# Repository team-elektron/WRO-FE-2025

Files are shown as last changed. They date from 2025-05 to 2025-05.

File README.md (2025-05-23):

# Elektron Team - WRO Future Engineers 2025

## Content

* `t-photos` contains 2 photos of the team (an official one and one funny photo with all team members)
* `v-photos` contains 6 photos of the vehicle (from every side, from top and bottom)
* `video` contains the video.md file with the link to a video where driving demonstration exists
* `schemes` contains schematic diagrams of the driving base.
* `src` contains code of control software for all components which were programmed to participate in the competition.
* `models` is for the files for models used by 3D printers to produce the vehicle elements.
* `other` is for other files which can be used to understand how to prepare the vehicle for the competition.

## Introduction

This is the public repository for our team and the work we have done on our robot.

<p float="left">
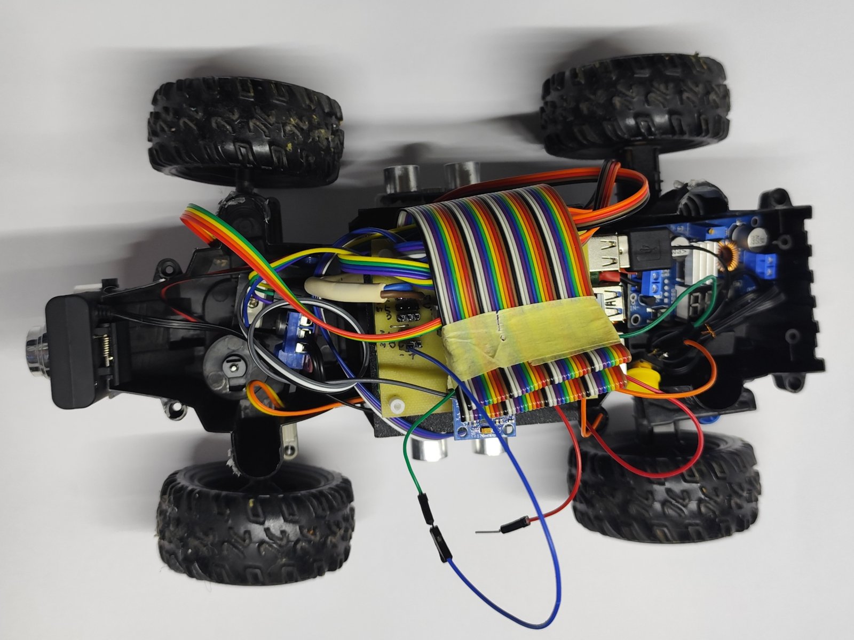
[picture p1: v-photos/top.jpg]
  
  &nbsp;
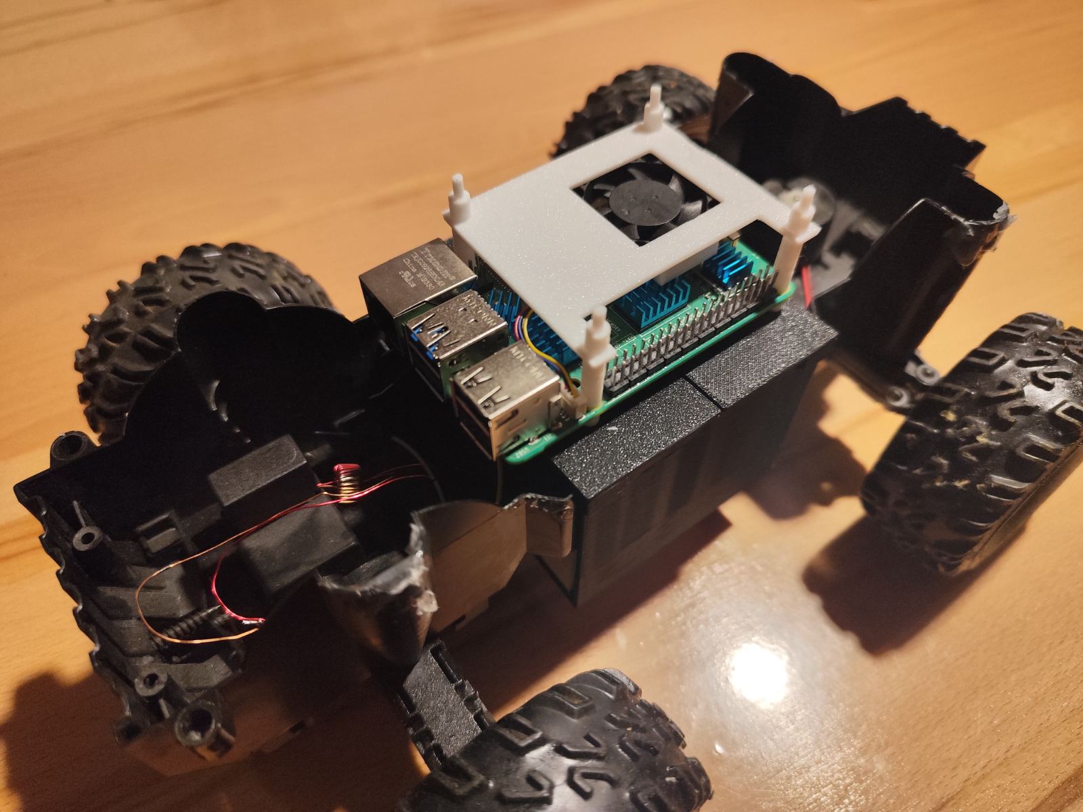
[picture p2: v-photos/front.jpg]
  
</p>

## Design elements

### Technical specifications
- Power: 3s1p Li-Ion Battery (EVE ICR18650-26v)
- Control: Raspberry Pi 5 8GB SBC
- Movement: Brushed motor
- Sensors: 3x Ultrasonic sensors, Camera

### Driving elements

For the driving base we have chosen a pre-made RC car driving base due to a lack of time. The steering and main driving motors are controled by a L298N Motor H-Bridge controller. 

<p float="left">
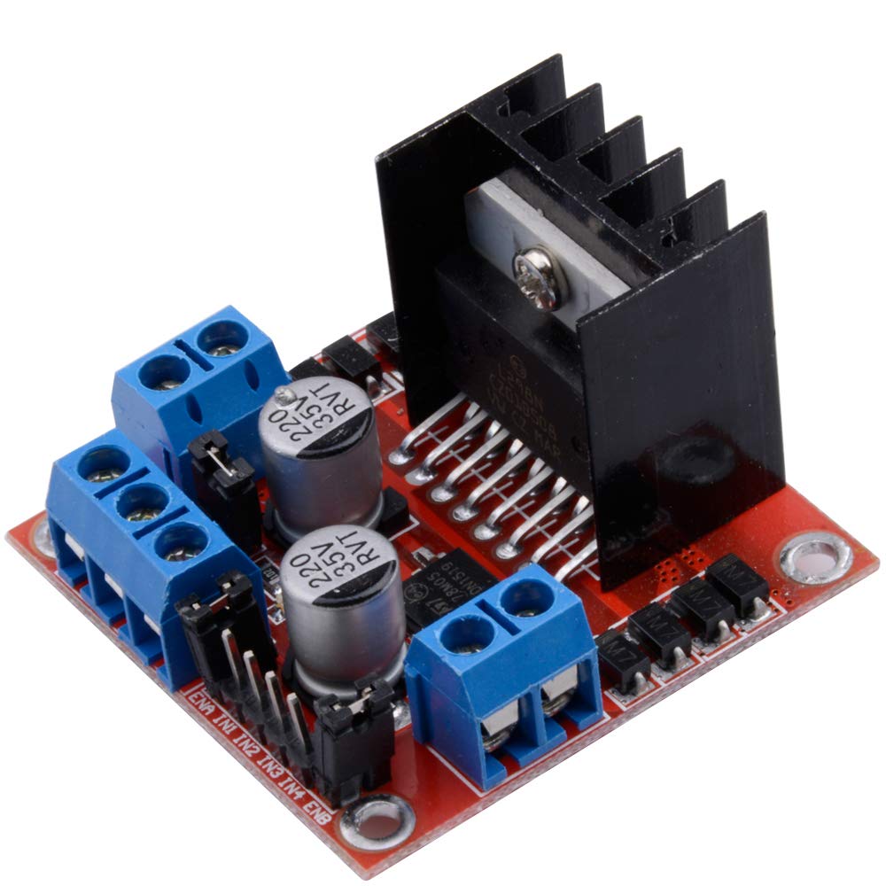
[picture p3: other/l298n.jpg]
  
</p>

### Cameras & Sensors

On our robot we have utilised a MPU-6050 IMU sensor for detecting the rotation angle when steering. 
The "eyes" of the operation are a set of 3 HC-SR04 Ultrasonic sensors and a standard USB Webcam.

<p float="left">
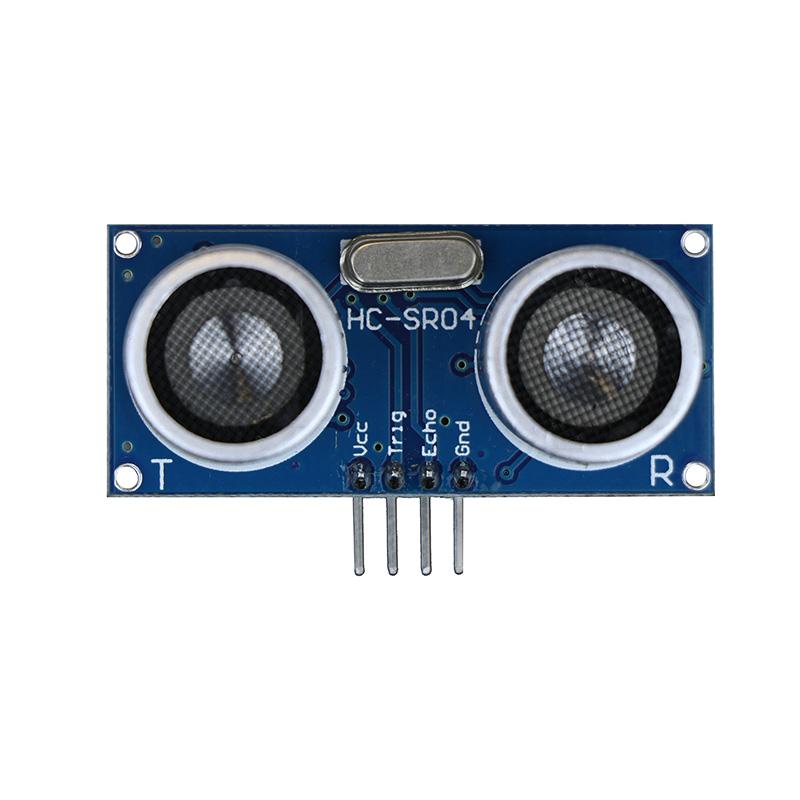
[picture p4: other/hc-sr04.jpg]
  
  &nbsp;
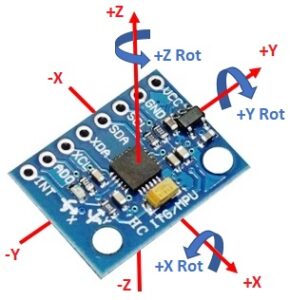
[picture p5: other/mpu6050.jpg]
  
  &nbsp;
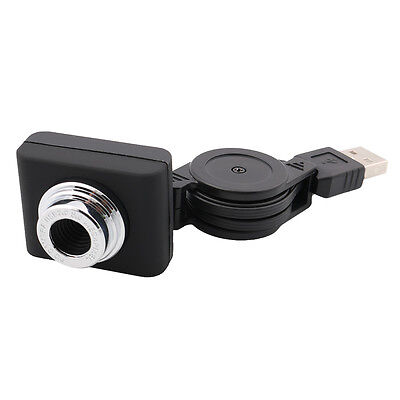
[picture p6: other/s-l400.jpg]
  
</p>

### Power supply and control elements

For the power supply we chose a custom made 18650 based battery in the 3s1p configuration which can be quickly charged with USB-C. 
This gives us around 27.5Wh (2.5Ah @ 10.8v nominal) to work with which is plenty for the job at hand.

<p float="left">
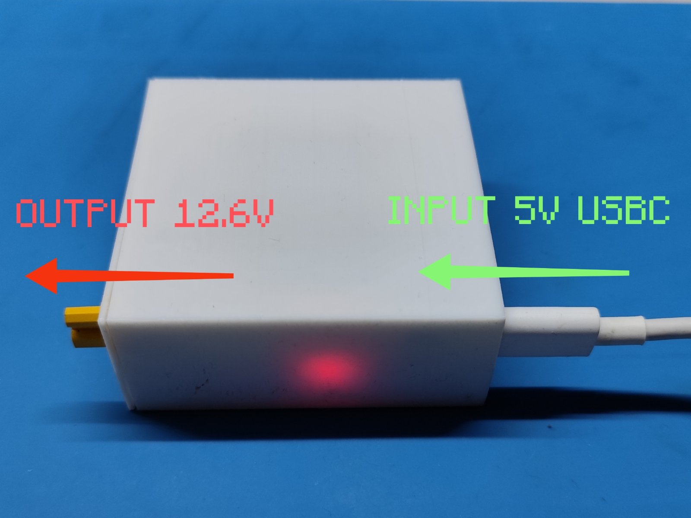
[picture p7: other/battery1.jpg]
  
  &nbsp;
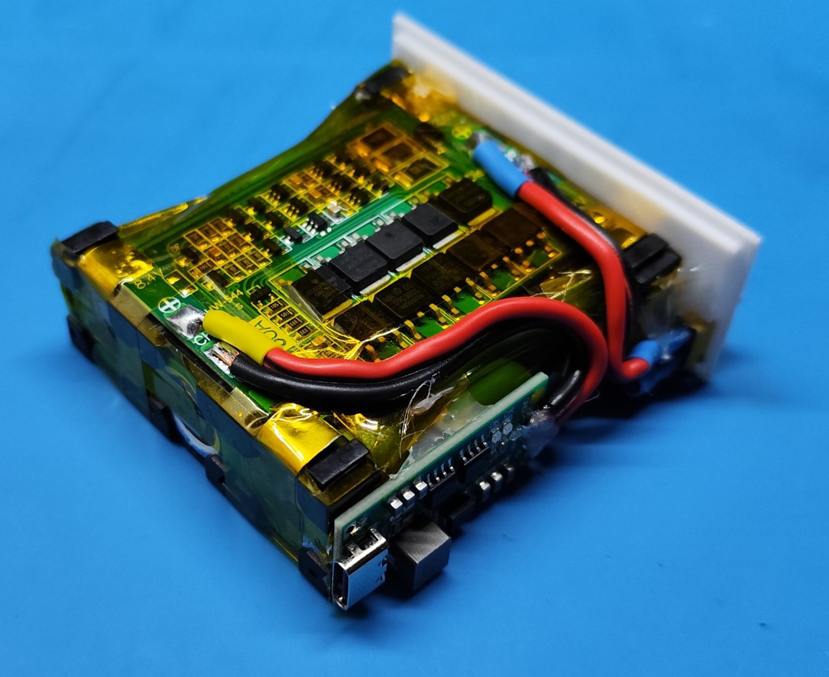
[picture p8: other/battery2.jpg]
  
</p>

The robot is based on a Raspberry Pi 5 which requires a stable power input of 5v @ 5A, for this job we have first chosen an UBEC voltage regulator, but due to the specific adapter we got not actually being able to handle the Pi, we had to switch to a more readily available replacement, the XL4015.

<p float="left">
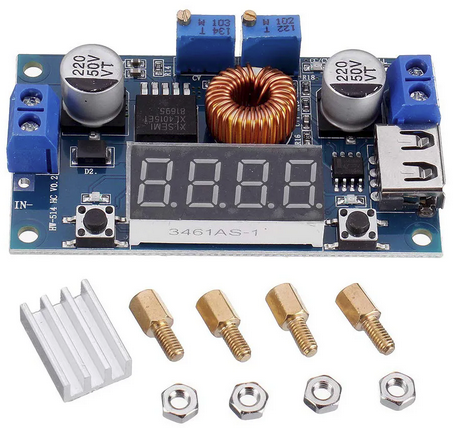
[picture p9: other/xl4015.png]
  
  &nbsp;
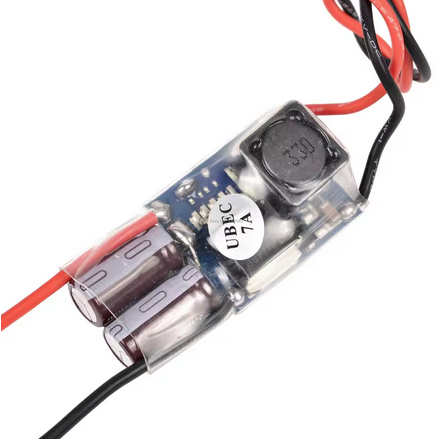
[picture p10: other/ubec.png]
  
</p>

We have designed a custom Pi GPIO shield to more easily wire up all of our power sources and sensors. The design for this PCB can be found in the schemes folder.

<p float="left">
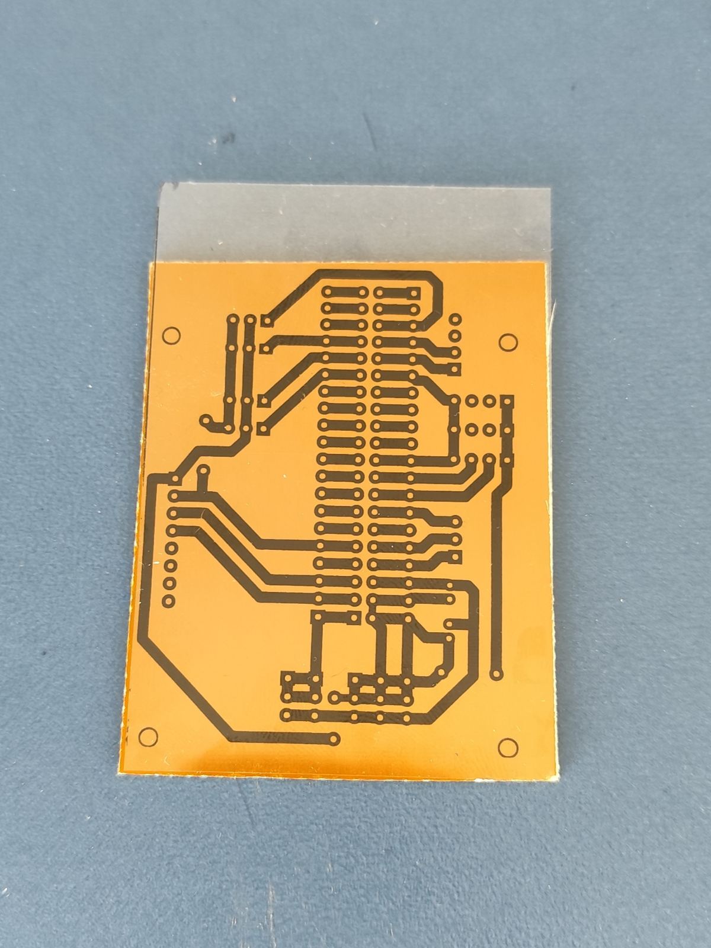
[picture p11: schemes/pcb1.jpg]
  
  &nbsp;
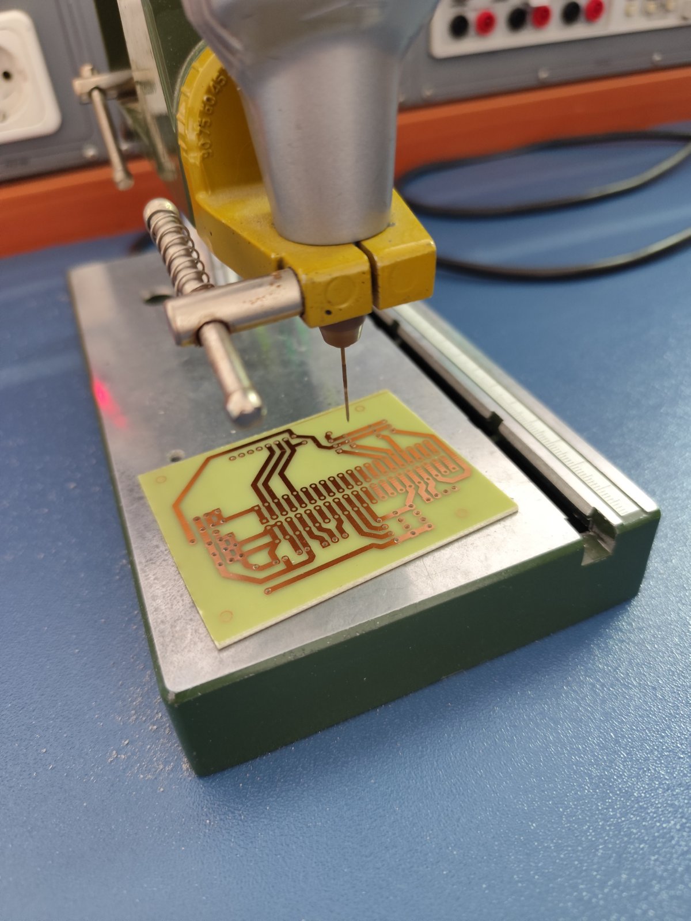
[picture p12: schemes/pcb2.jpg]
  
  &nbsp;
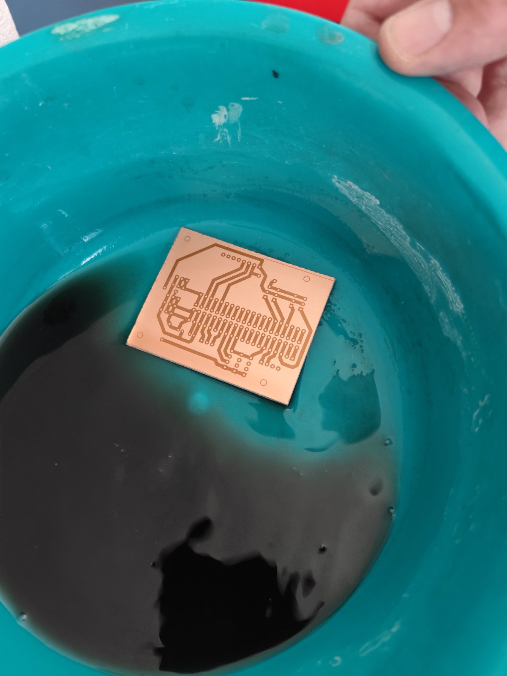
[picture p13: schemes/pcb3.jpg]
  
  &nbsp;
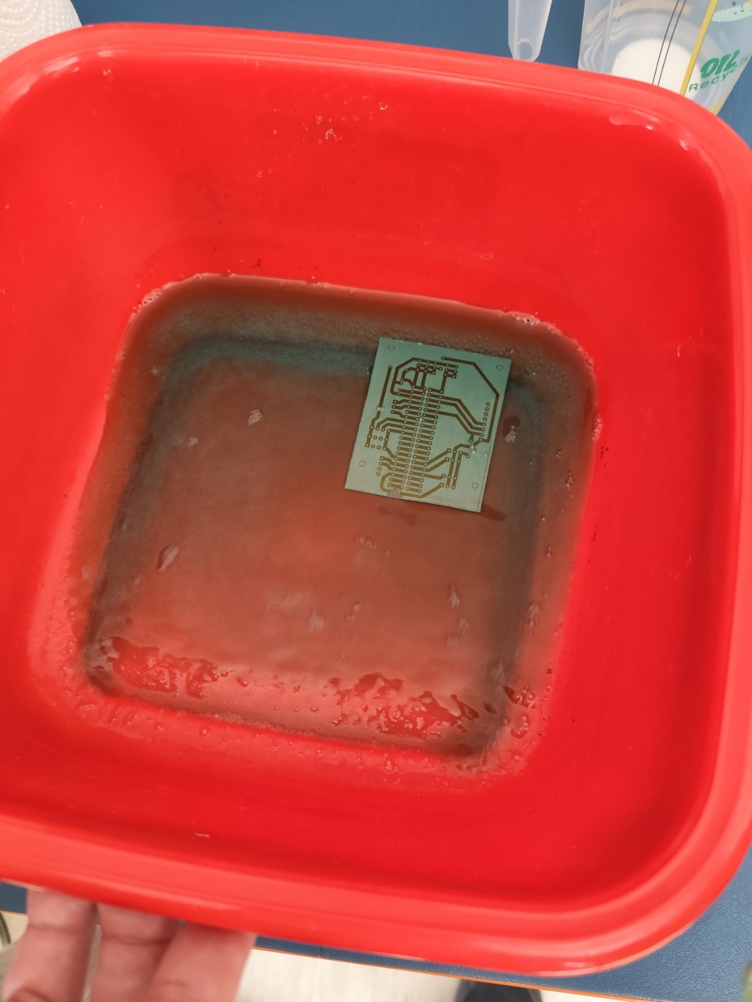
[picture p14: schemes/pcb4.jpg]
  
</p>

### Code

We have written our code in C++ using the WiringPi library for interfacing the Pi GPIO. 
You can find the code in the src folder and the instructions on how to use it.

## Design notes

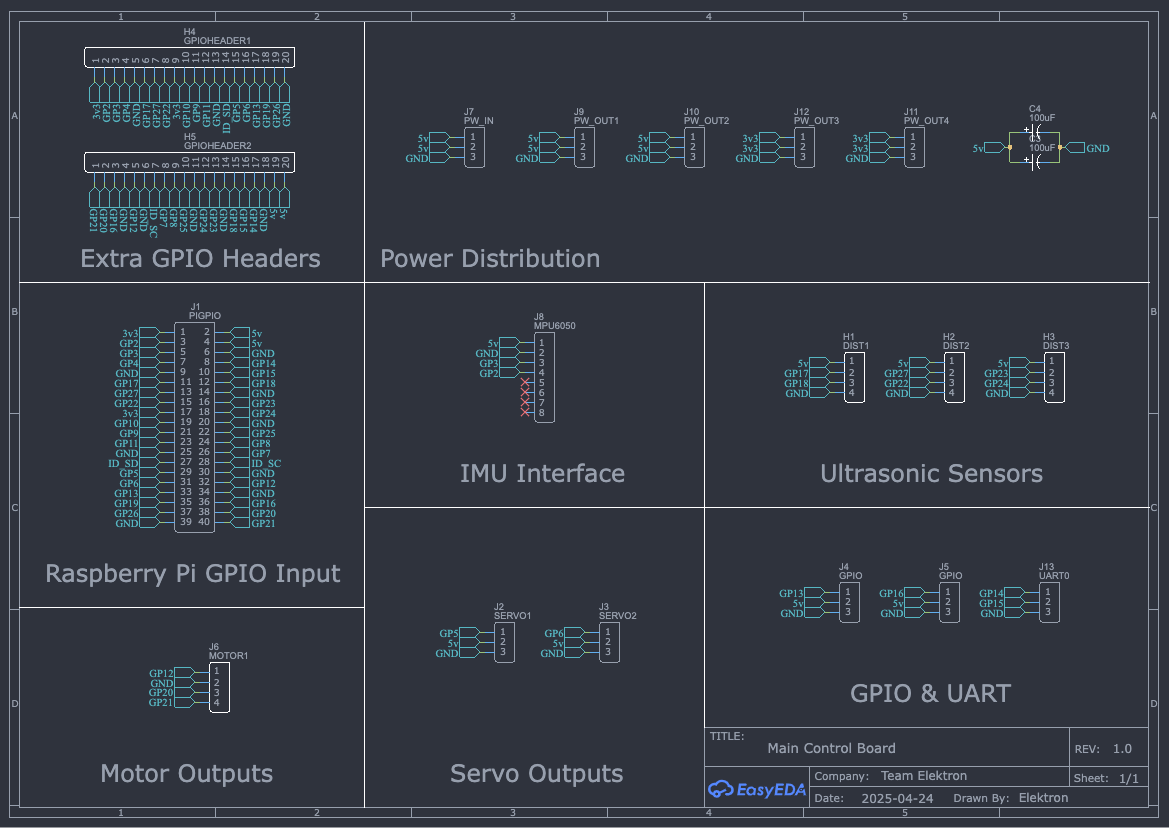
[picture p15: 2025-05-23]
schemes/Schematic_WRO FE Robot Control Board_2025-04-24.png

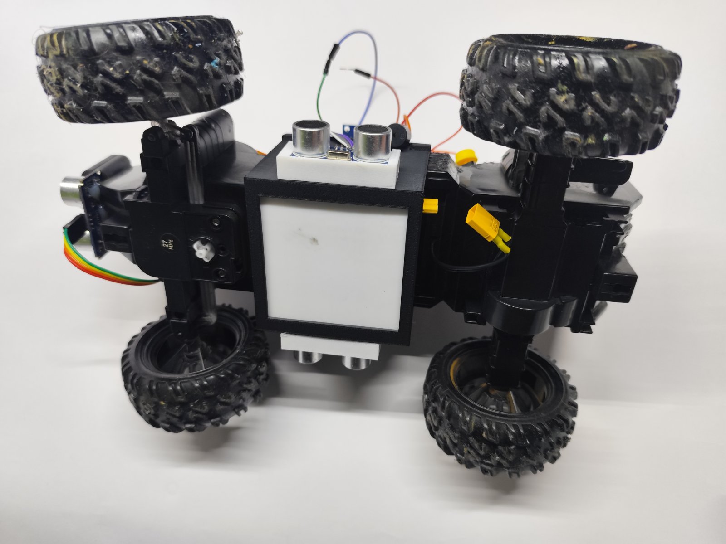
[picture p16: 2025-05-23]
v-photos/bottom.jpg

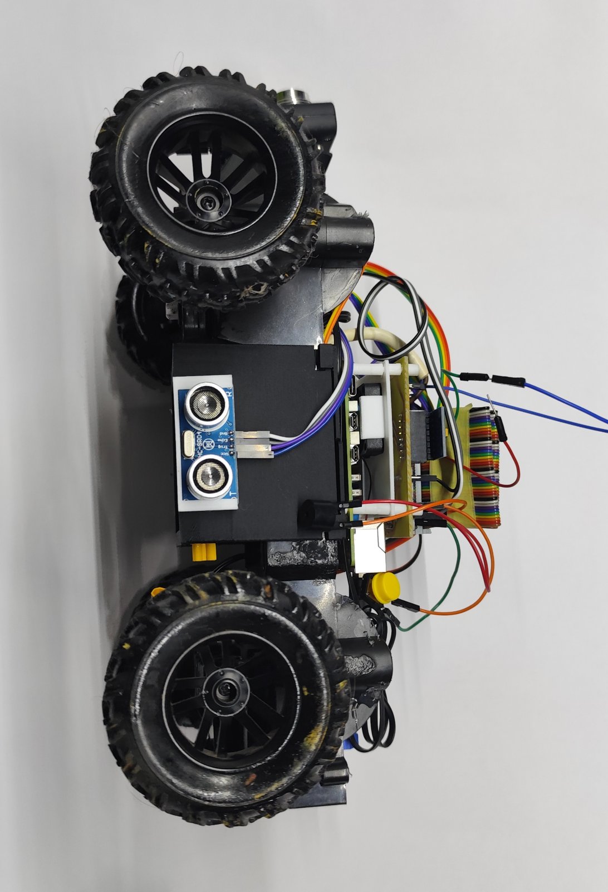
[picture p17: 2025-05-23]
v-photos/side2.jpg

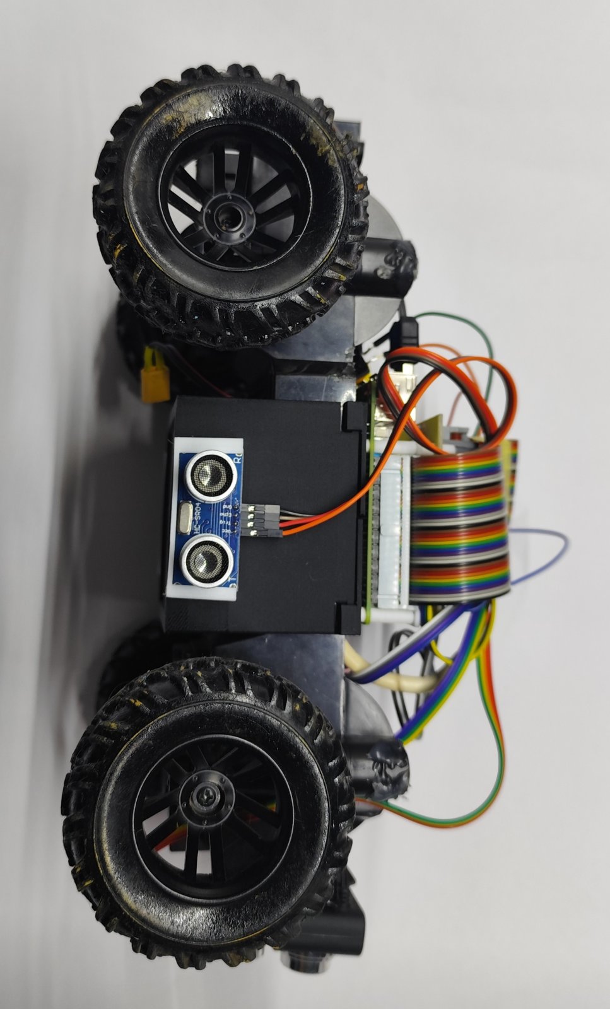
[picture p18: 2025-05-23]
v-photos/side1.jpg

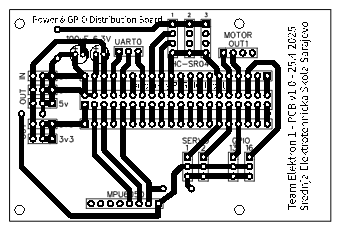
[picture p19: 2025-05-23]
schemes/PCB_PCB_WRO FE Robot Control Board_2025-04-25.png

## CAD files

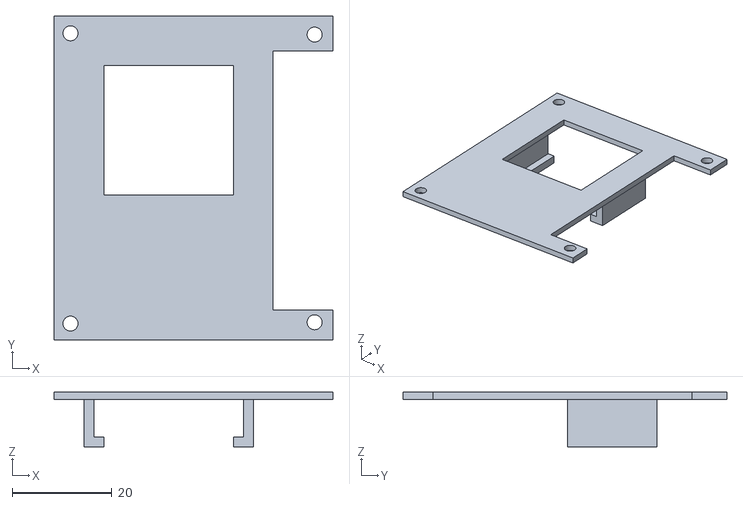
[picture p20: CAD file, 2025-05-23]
models/pi_fan.stl
56.0 x 65.0 x 11.0

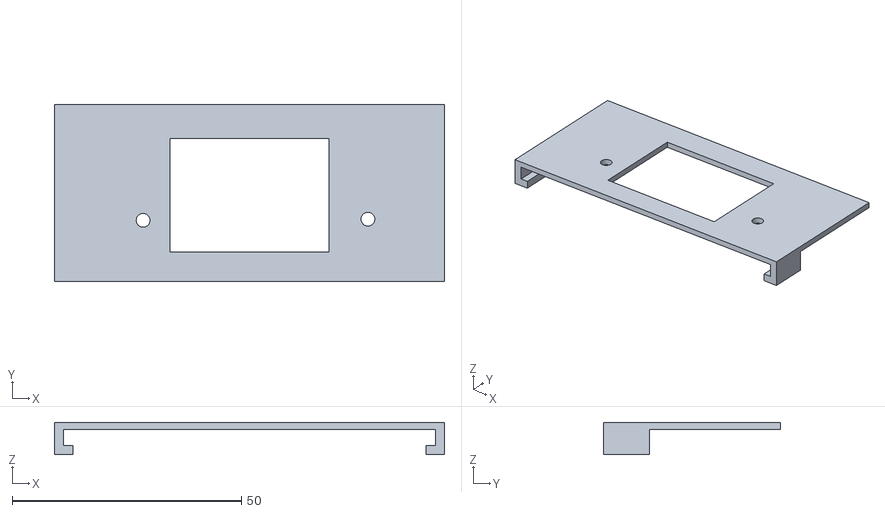
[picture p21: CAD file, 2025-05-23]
models/batteryholder_cover1.stl
85.0 x 38.5 x 7.00

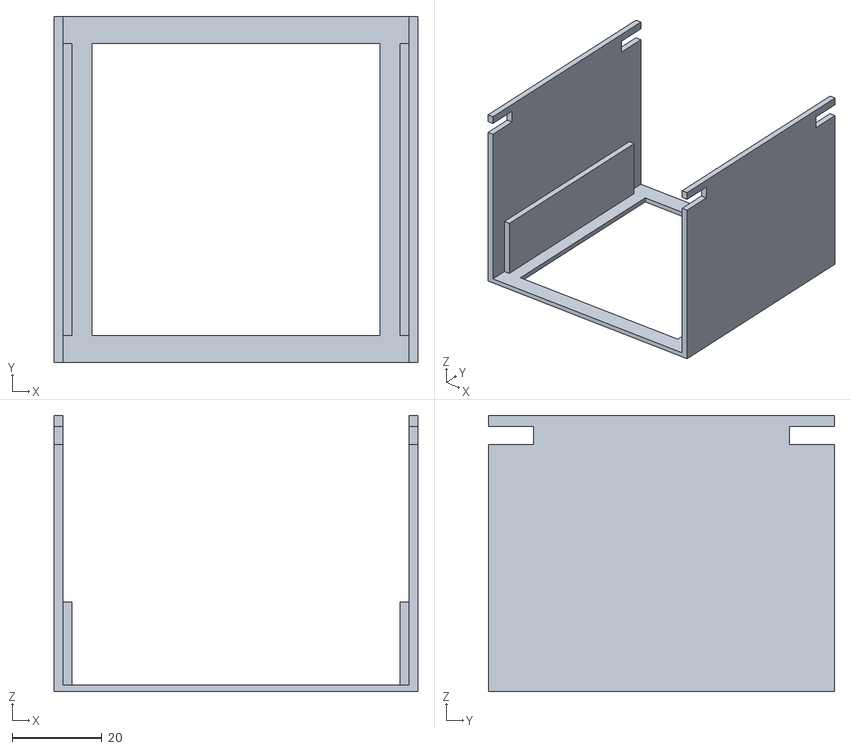
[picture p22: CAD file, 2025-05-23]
models/batteryholder_bottom.stl
81.0 x 77.0 x 61.5

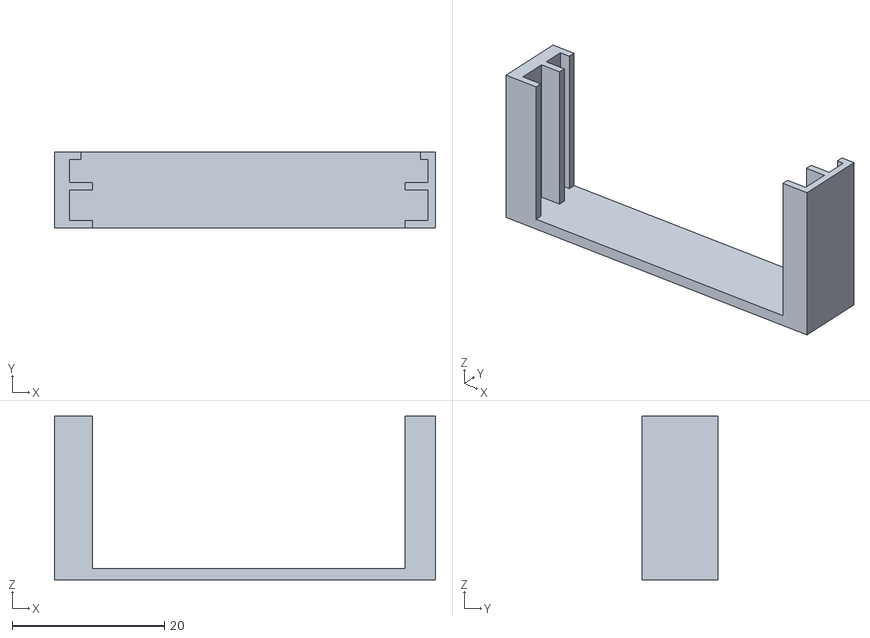
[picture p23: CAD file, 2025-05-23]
models/side hc-sr04.stl
50.0 x 10.0 x 21.5

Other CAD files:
models/batteryholder_cover2.stl

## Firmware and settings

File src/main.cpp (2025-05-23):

#include <iostream>
#include <unistd.h>
#include "MPU6050.h"
#include "Ultrasonic.h"
#include "wiringPi.h"
#include <softPwm.h>

int main() {
    wiringPiSetupGpio();  // Enables BCM numbering

    pinMode(12, OUTPUT);
    pinMode(16, OUTPUT);
    pinMode(21, OUTPUT);
    pinMode(20, OUTPUT);
    pinMode(5, OUTPUT);
    pinMode(13, OUTPUT);
    pinMode(19, OUTPUT);
    pinMode(26, INPUT);
    pullUpDnControl(26, PUD_UP);      // Enable internal pull-up resistor

    int gomode = 0;

    int ENAPin = 12; // BCM 12
    softPwmCreate(12, 0, 100); // Pin 12, initial 0, range 0–100
    int ENBPin = 16; // BCM 16
    softPwmCreate(16, 0, 100); // Pin 16, initial 0, range 0–100


    std::cout << "Starting sensor loop" << std::endl;

    MPU6050 mpu6050;
    mpu6050.begin();

    Ultrasonic sensor1(23, 24);  // Trig, Echo
    Ultrasonic sensor2(27, 22);
    Ultrasonic sensor3(17, 18);

    while (true) {
        mpu6050.update();
        float angle = mpu6050.angle();
        float dist1 = sensor1.distanceCM();
        float dist2 = sensor2.distanceCM();
        float dist3 = sensor3.distanceCM();

        std::cout << "Angle: " << angle
                  << " | Distances: "
                  << dist1 << "cm, "
                  << dist2 << "cm, "
                  << dist3 << "cm"
                  << std::endl;


        if (dist1 >= 100 && gomode == 0) {
            std::cout << "cmar" << std::endl;
            softPwmWrite(ENAPin, 25); // 50% duty cycle
            digitalWrite(21, HIGH); 
            digitalWrite(20, LOW); 

            if (dist2 <= 30) {
                digitalWrite(19, HIGH);
                softPwmWrite(16, 35);
                digitalWrite(5, HIGH);
                digitalWrite(13, LOW);
            } else {
                digitalWrite(19, LOW);
                softPwmWrite(16, 35);
                digitalWrite(5, LOW);
                digitalWrite(13, HIGH);
            }
        } else {
            if (gomode == 0) {
                softPwmWrite(16, 0);
                softPwmWrite(12, 50);
                digitalWrite(21, LOW);  
                digitalWrite(20, HIGH);  
                delay(100);
                softPwmWrite(12, 0); // 50% duty cycle
                digitalWrite(21, LOW);  
                digitalWrite(20, LOW);  
                gomode = 1;
                mpu6050.resetAngle();
            } else {}
            //usleep(1000);
            std::cout << gomode << std::endl;
                if (angle >= -90 && gomode == 1) {
                    softPwmWrite(16, 35);
                    digitalWrite(5, HIGH);
                    digitalWrite(13, LOW);
                    usleep(10000);
                    softPwmWrite(12, 29); // 50% duty cycle
                    digitalWrite(21, HIGH);  
                    digitalWrite(20, LOW);  
                } else {
                    softPwmWrite(16, 0);
                    softPwmWrite(12, 100); // 50% duty cycle
                    digitalWrite(21, LOW);  
                    digitalWrite(20, LOW);  
                    usleep(10000);
                    softPwmWrite(12, 0); // 50% duty cycle
                    digitalWrite(21, LOW);  
                    digitalWrite(20, LOW);  
                    //break;
                    gomode = 0;
                }
            
        }
        //std::cout << gomode << std::endl;

        usleep(50000);  // 50ms delay
        
    }

    return 0;
}

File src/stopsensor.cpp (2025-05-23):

#include <iostream>
#include <wiringPi.h>
#include "libraries/MPU6050.h"
#include "libraries/Ultrasonic.h"

int main() {
    wiringPiSetupGpio(); // Use BCM GPIO numbers instead

    pinMode(12, OUTPUT); // Main motor ENA
    pinMode(16, OUTPUT);
    pinMode(21, OUTPUT); // Main motor IN2 (Forward)
    pinMode(20, OUTPUT); // Main motor IN1 (Backward)




    while (true) {
        digitalWrite(16, LOW); // 50% duty cycle
        digitalWrite(5, LOW); // LED on
        digitalWrite(13, LOW); // LED on
        digitalWrite(12, LOW); // LED on
        digitalWrite(21, LOW); // LED on
        digitalWrite(20, LOW); // LED 
    }

    return 0;
}
